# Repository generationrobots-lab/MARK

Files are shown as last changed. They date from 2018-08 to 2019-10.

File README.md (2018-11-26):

# M.A.R.K

M.A.R.K est un robot modulaire destiné à l'apprentissage. La carte [Arduino Mega] et la librairie fournie permettent une utilisation simple des principaux modules. L'[IDE Arduino] procure les outils nécessaires pour programmer le micro-contrôleur de la carte [Arduino Mega], le celèbre [ATmega2560]. 

[IDE Arduino]: https://www.arduino.cc/en/Main/Software/
[Arduino Mega]:https://www.generationrobots.com/fr/401945-arduino-mega-2560-rev3.html
[ATmega2560]: http://ww1.microchip.com/downloads/en/devicedoc/atmel-2549-8-bit-avr-microcontroller-atmega640-1280-1281-2560-2561_datasheet.pdf

## Installation

### IDE Arduino
Page de téléchargement : <br />
https://www.arduino.cc/en/Main/Software

Tutoriels d'installation : <br />
https://www.arduino.cc/en/Guide/Windows<br />
https://www.arduino.cc/en/Guide/Linux <br />
Le paquet Arduino est également présent dans les dépôts Universe d'Ubuntu.

### M.A.R.K librairie

1. [Télécharger le git](https://github.com/generationrobots-lab/MARK/archive/master.zip)
2. Décompresser l'archive et la placer dans un répertoire de votre choix.
3. Lancer l'IDE Arduino 
4. Dans  `Fichier => Préférences => Paramètres`, le champ "Emplacement du carnet de croquis" doit pointer vers le dossier "Software" de l'archive fraîchement décompressée et rangée (exemple : D:\MARK-master\Software)
5. Dans l'IDE Arduino, vous devriez voir apparaitre dans `Ficher => Exemples => MARK` les exemples pour débuter avec votre M.A.R.K.

Il est également possible de fusionner le dossier Software avec le dossier que vous utilisez déjà (par defaut C:\Users\..\Documents\Arduino).

## Code d'exemple 

```c++
#include <MARK.h>

MARK myrobot; //initialize an instance of the class

void setup() {
  myrobot.begin();
  delay(50);
  myrobot.setLeftMotor(50);
  myrobot.setRightMotor(50);
  delay(3000); //forward 3s
  myrobot.stopLeftMotor();
  myrobot.stopRightMotor();
}

void loop() {
  //nothing
  delay(300);
}

```

## Documentation
Pour plus d'informations, merci de consulter le [wiki.](https://github.com/generationrobots-lab/MARK/wiki)

## Developement

### Contribution

Pour toute contribution au maintien ou à l'amélioration de la librairie, merci de faire un "pull request".  <br />
Pour remonter des problèmes, merci d'ouvrir un ticket dans les "issues".

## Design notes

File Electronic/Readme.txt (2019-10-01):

YOu need to import all of libreries in your eagle folder and after open the schematic MARK.sch

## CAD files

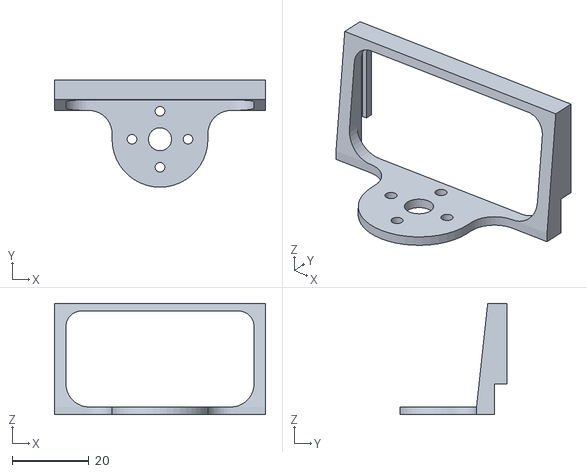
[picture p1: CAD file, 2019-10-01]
3D_model/US_Support.STL
55.0 x 28.0 x 29.0

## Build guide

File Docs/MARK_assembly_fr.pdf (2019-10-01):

# M.A.R.K

### By Génération Robots

10/09/2018

# Documentation de montage

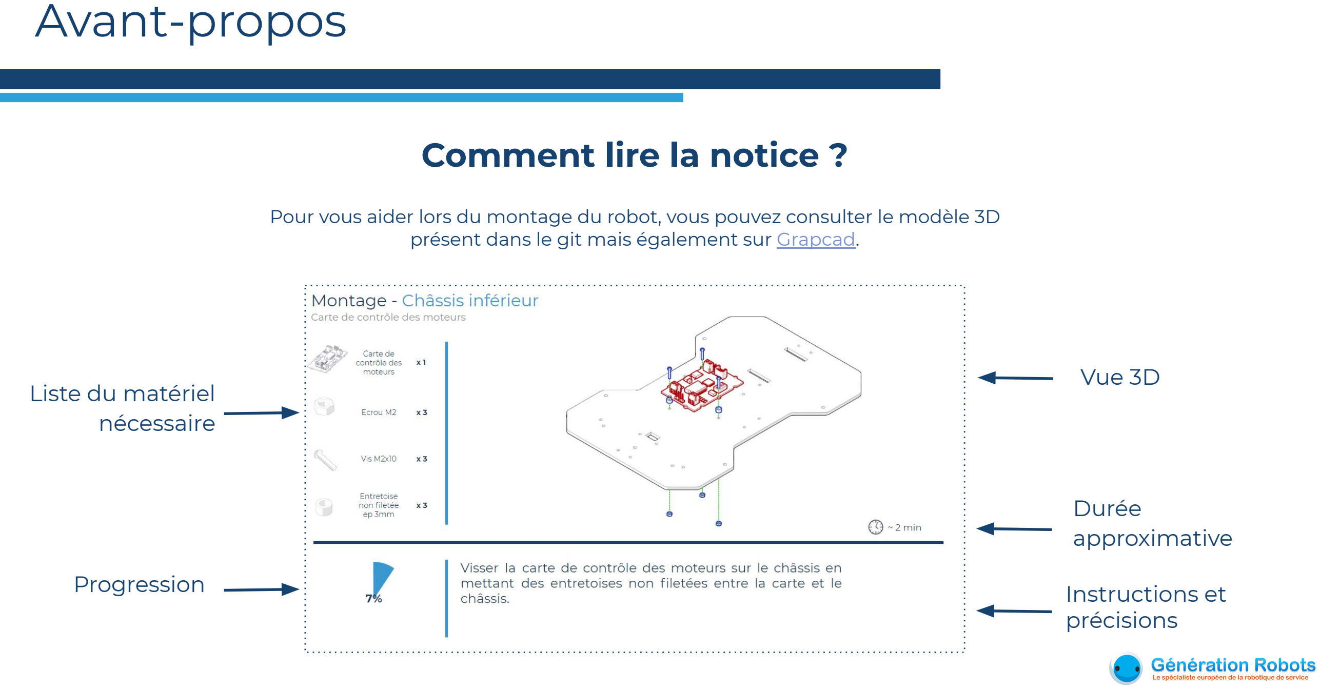
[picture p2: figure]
Avant-propos; Comment lire la notice ?; Instructions et précisions; Vue 3D; Durée approximative; Progression; Liste du matériel nécessaire

Pour vous aider lors du montage du robot, vous pouvez consulter le modèle 3D présent dans le git mais également sur Grapcad. (https://grabcad.com/library/m-a-r-k-1)

### Montage - Châssis inférieur

Vue globale

3

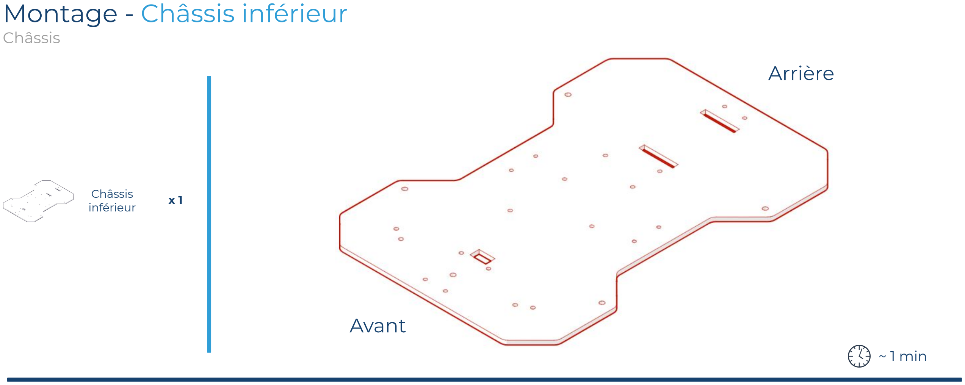
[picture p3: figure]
~ 1 min; Châssis; inférieur; Avant; Arrière; Montage - Châssis inférieur

Prendre le châssis inférieur.
Pour repérer le sens, la gravure dans le coin est à l’arrière gauche du robot et est dans le bon sens de lecture si on se place au dessus du châssis.

2%

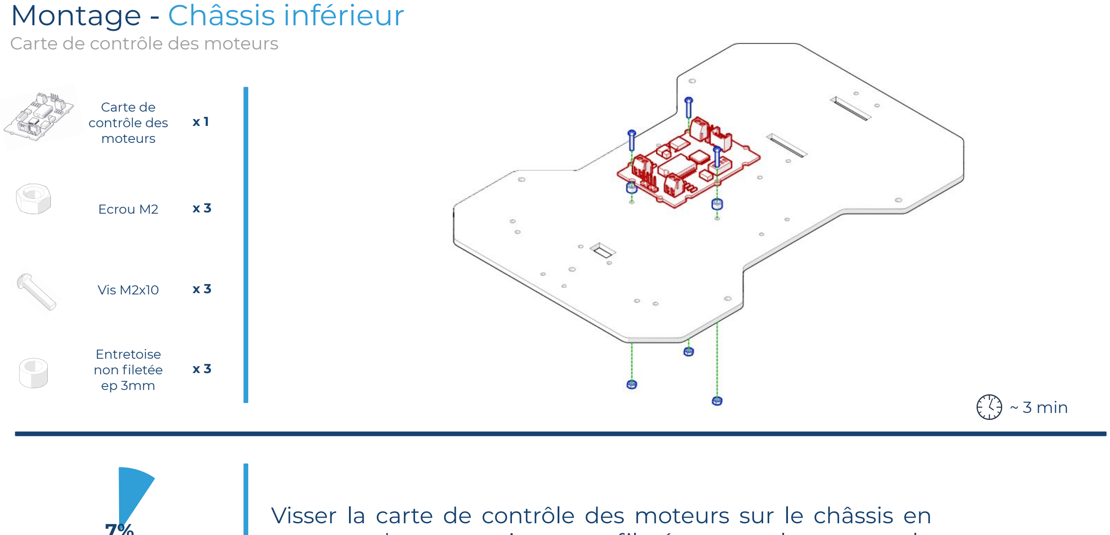
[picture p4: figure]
Montage - Châssis inférieur; Carte de contrôle des moteurs; ~ 3 min; Ecrou M2; Vis M2x10; Entretoise non filetée ep 3mm

Visser la carte de contrôle des moteurs sur le châssis en mettant des entretoises non filetées entre la carte et le châssis.

7%

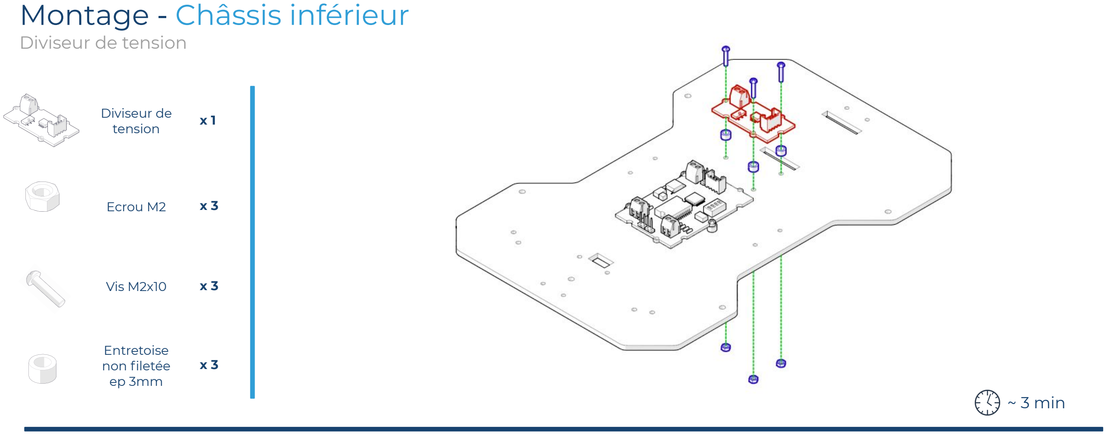
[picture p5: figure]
Diviseur de; tension; ~ 3 min; Entretoise non filetée ep 3mm; Montage - Châssis inférieur; Diviseur de tension; Ecrou M2; Vis M2x10

Visser le diviseur de tension sur le châssis en mettant des entretoises non filetées entre la carte et le châssis.
12%

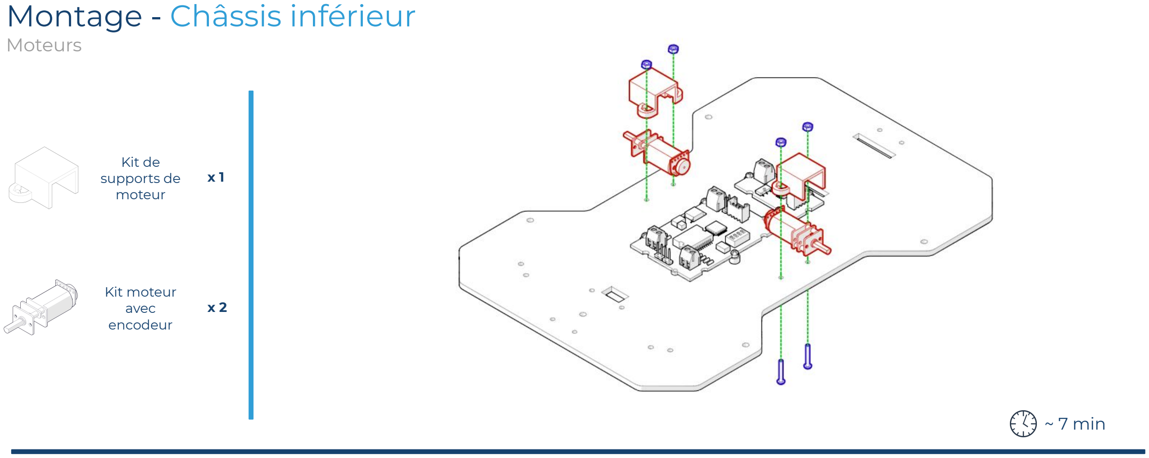
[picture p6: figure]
Kit de supports de moteur; ~ 7 min; Kit moteur avec encodeur; Montage - Châssis inférieur; Moteurs

Fixer les moteurs à l’aide des supports.
Les encoches à l'intérieur du support correspondent aux plaques présentes dans la partie réducteur du moteur. Placer l’écrou dans le logement prévu à cet effet dans le support avant de visser.

18%

Brancher les moteurs (via les encodeurs) sur la carte de contrôle des moteurs.

Retirer le jumper (J4) et vérifier l’adresse I2C.

18%

~ 5 min

### Montage - Châssis supérieur

Câblage

Monter les roues sur les moteurs.

20%

~ 2 min

x 2 Roue
60 x 8mm

### Montage - Châssis inférieur

Roues motrices

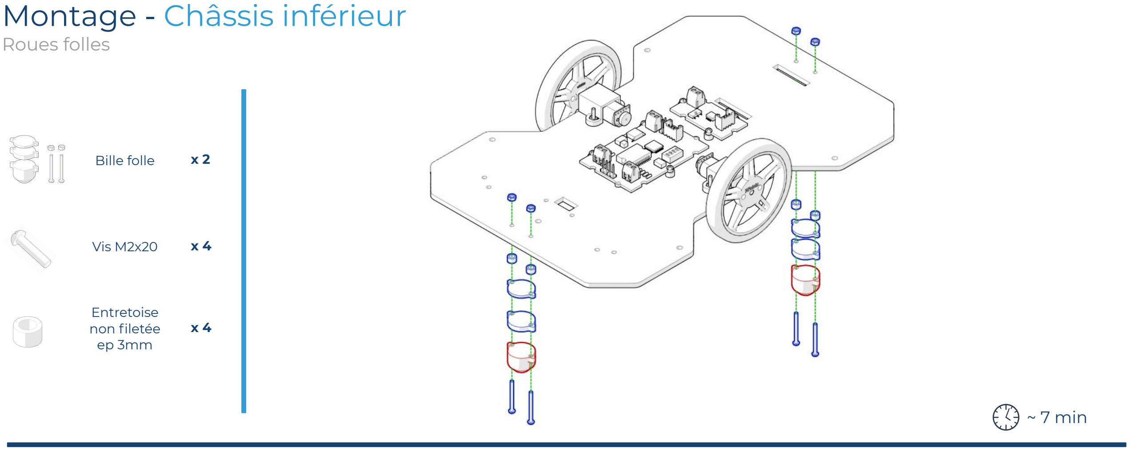
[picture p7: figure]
Bille folle; ~ 7 min; Entretoise non filetée ep 3mm; Vis M2x20; Montage - Châssis inférieur; Roues folles

Monter les billes sous le châssis en utilisant tous les éléments présents dans le sachet et deux entretoises non filetées (ep 3mm).
25%

### Montage - Châssis inférieur

Microrupteurs

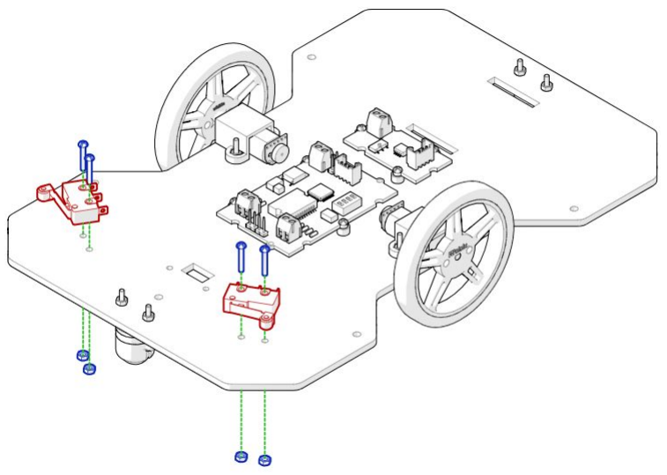
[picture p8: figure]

Visser les microrupteurs sur le châssis en prenant soin que les galets soient tournés vers l'extérieur du robot.

~ 4 min

30%

microrupteur x 2

x 4

Ecrou M2 x 4

Vis M2x6

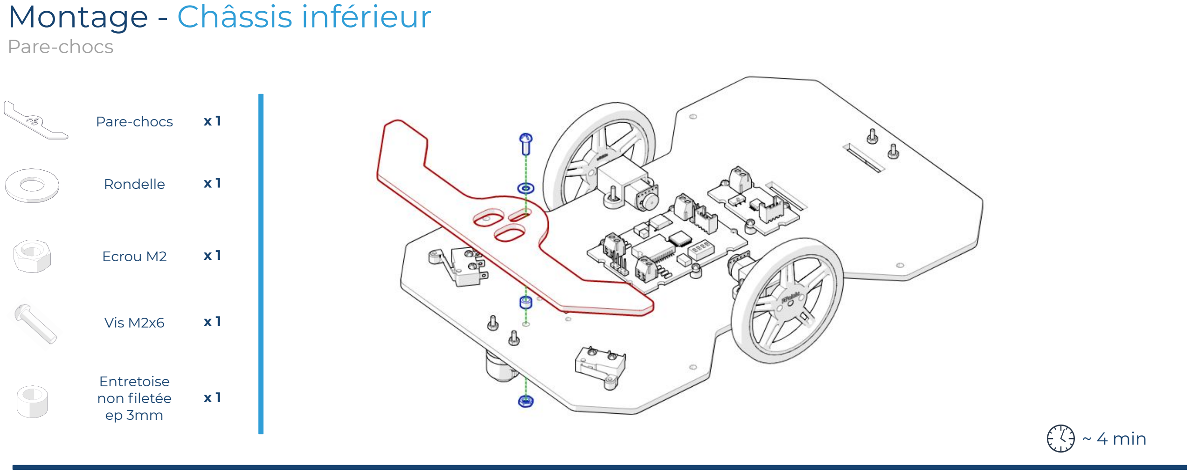
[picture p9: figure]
Rondelle; ~ 4 min; Ecrou M2; Vis M2x6; Entretoise non filetée ep 3mm; Montage - Châssis inférieur; Pare-chocs

Monter le pare-choc en mettant une entretoise non filetée dans le trou oblong, la rondelle par dessus et enfin visser le tout. le pare-choc doit rester mobile.
30%

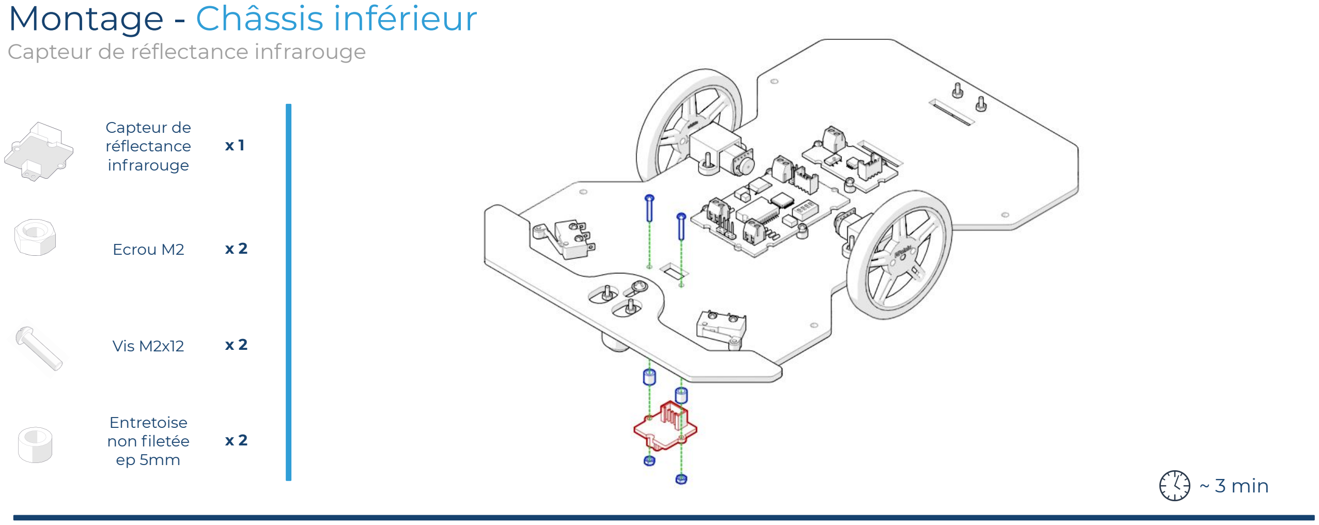
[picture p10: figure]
Capteur de réflectance infrarouge; ~ 3 min; Ecrou M2; Vis M2x12; Entretoise non filetée ep 5mm; Montage - Châssis inférieur

Visser le capteur de réflectance infrarouge sous le châssis en mettant des entretoises non filetées entre la carte et le châssis.
34%

Visser les grandes entretoises filetées au châssis.

~ 2 min

### Montage - Châssis inférieur

Entretoises

36%

Entretoise M3
F/F 60mm | x 4
Vis M3 x 8mm | x 4

### Montage - Châssis supérieur

Vue globale

15

### Montage - Châssis supérieur

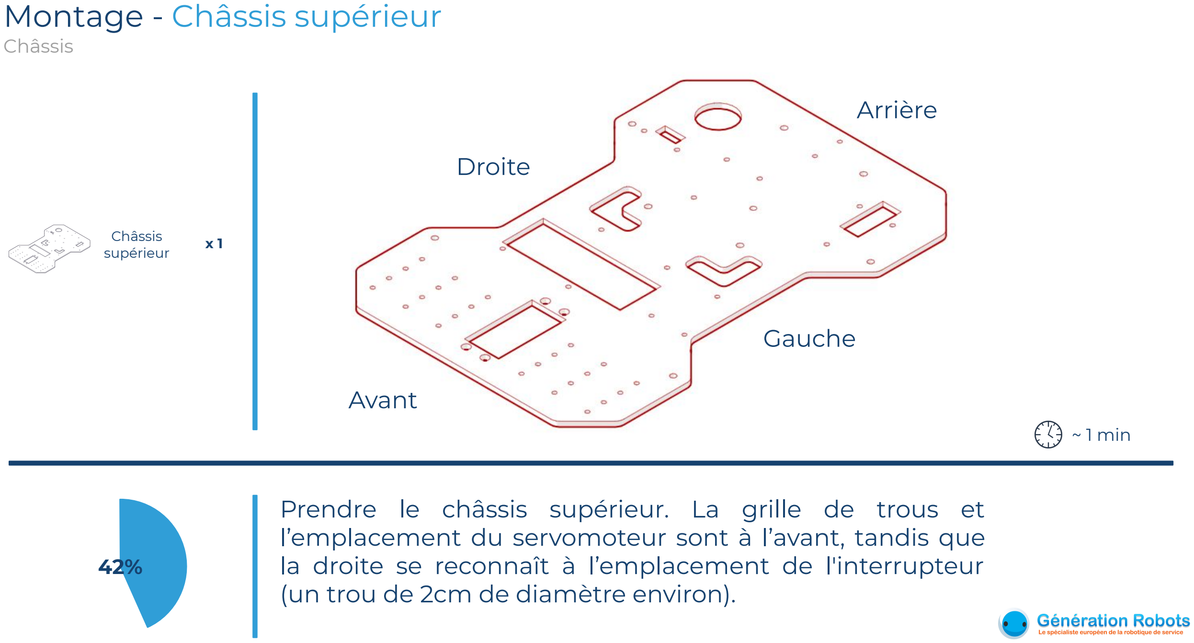
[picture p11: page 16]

Prendre le châssis supérieur. La grille de trous et l’emplacement du servomoteur sont à l’avant, tandis que la droite se reconnaît à l’emplacement de l'interrupteur (un trou de 2cm de diamètre environ).

~ 1 min

Châssis

Avant

Arrière

Droite

Gauche

42%

Châssis
supérieur x 1

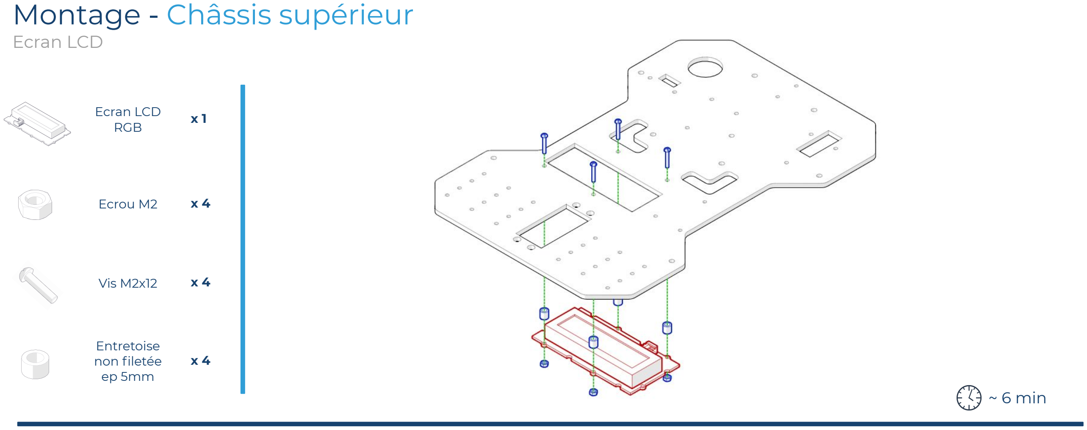
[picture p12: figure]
Ecran LCD RGB; ~ 6 min; Ecrou M2; Vis M2x12; Entretoise non filetée ep 5mm; Montage - Châssis supérieur; Ecran LCD

Connecter | le | câble | avant | de | monter | l’écran.

Visser l’écran LCD sous le châssis en mettant des entretoises non filetées entre la carte et le châssis.

47%

Visser le module wifi sous le châssis, les composants vers le bas.

~ 4 min

### Montage - Châssis supérieur

Module Wifi

51%

Module wifi x 1

x 3

Ecrou M2 x 4

Vis M2x6

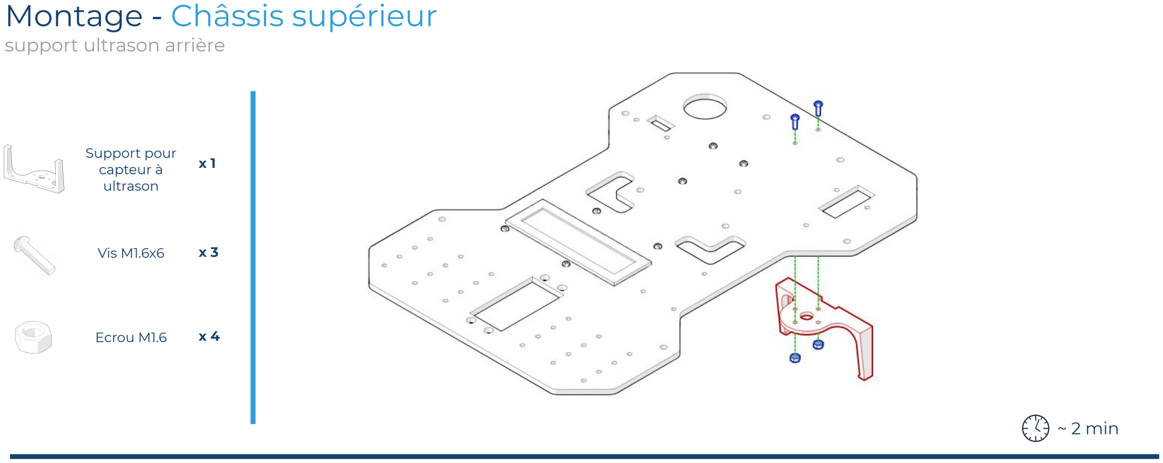
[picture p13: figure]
~ 2 min; Montage - Châssis supérieur; support ultrason arrière; Support pour capteur à ultrason; Ecrou M1.6; Vis M1.6x6

Visser un premier support pour capteur à ultrason à l’arrière du robot.
55%

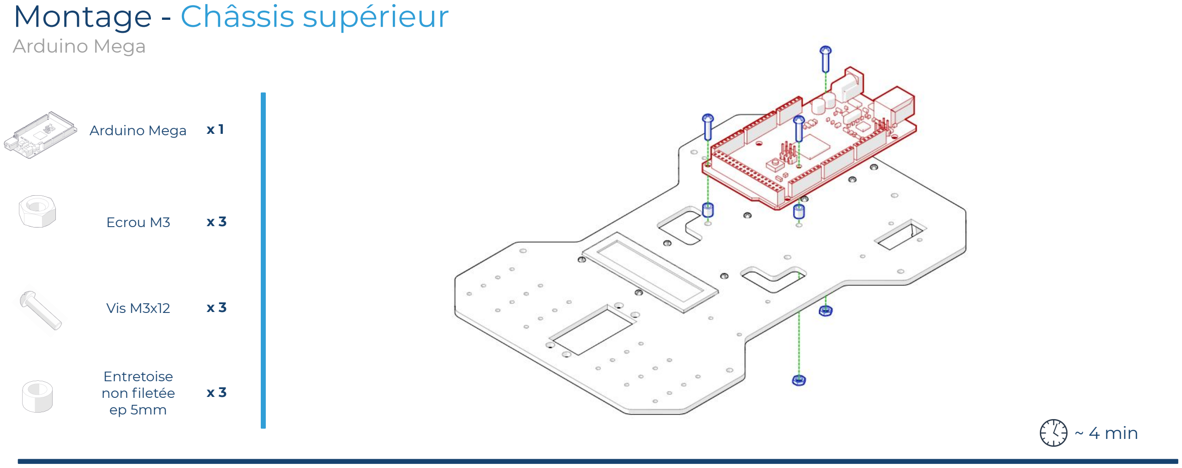
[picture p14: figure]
Arduino Mega; ~ 4 min; Ecrou M3; Vis M3x12; Entretoise non filetée ep 5mm; Montage - Châssis supérieur

Visser l’arduino mega sur le châssis en mettant des entretoises non filetées entre la carte et le châssis.
60%

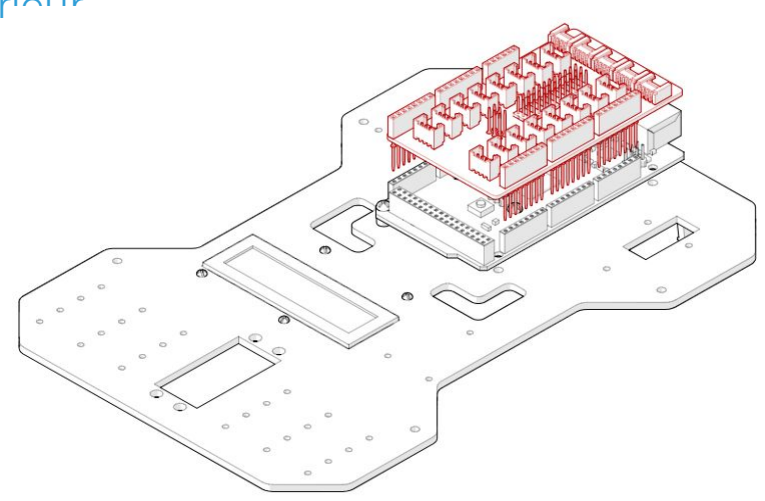
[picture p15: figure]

Mettre en place le grove mega shield sur l’arduino mega en s’assurant que les broches correspondent.

~ 1 min

### Montage - Châssis supérieur

Mega Shield

65%

Mega Shield x 1

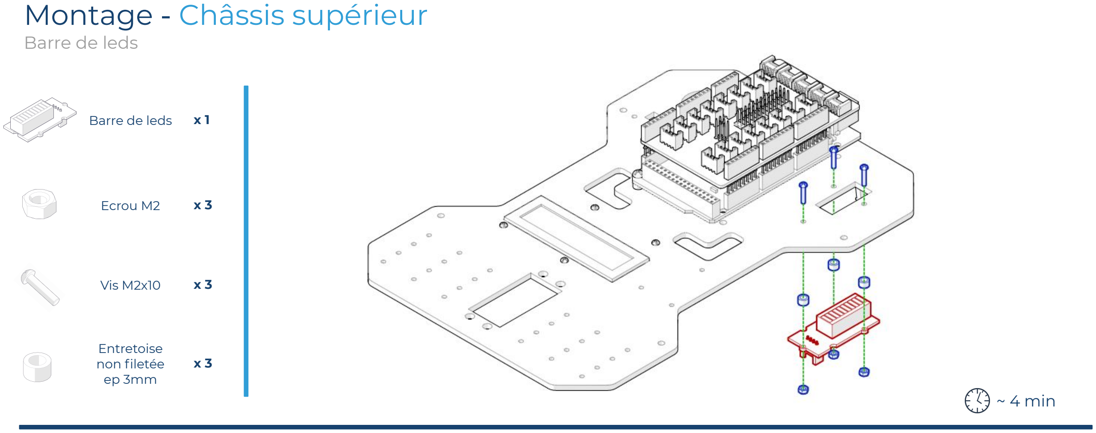
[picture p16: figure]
Barre de leds; ~ 4 min; Ecrou M2; Vis M2x10; Entretoise non filetée ep 3mm; Montage - Châssis supérieur

Visser la barre de leds sous le châssis en mettant des entretoises non filetées entre la carte et le châssis.
70%

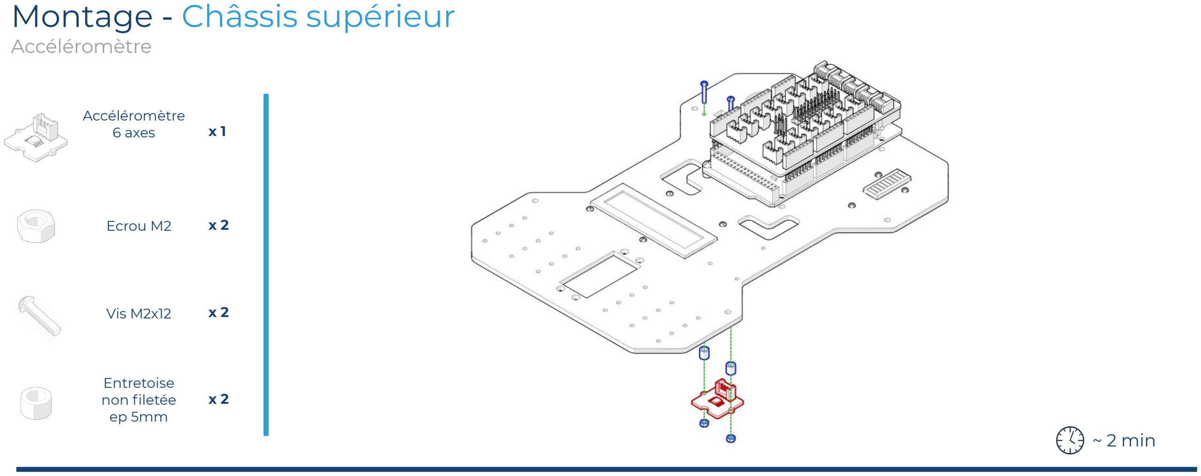
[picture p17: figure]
Accéléromètre 6 axes; ~ 2 min; Ecrou M2; Vis M2x12; Entretoise non filetée ep 5mm; Montage - Châssis supérieur; Accéléromètre

Visser l'accéléromètre sous le châssis en mettant des entretoises non filetées entre la carte et le châssis.
73%

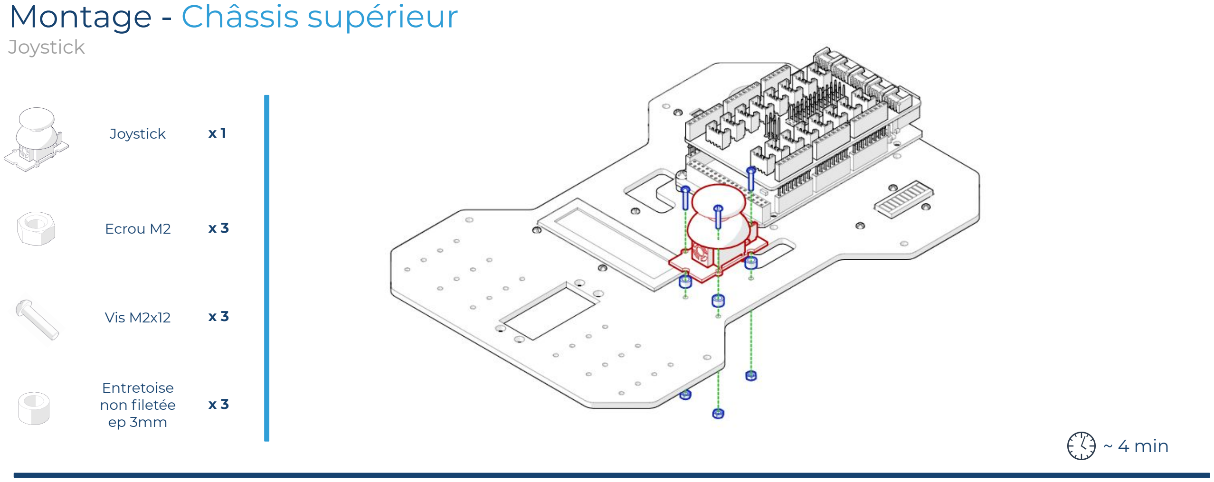
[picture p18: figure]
Joystick; ~ 4 min; Ecrou M2; Vis M2x12; Entretoise non filetée ep 3mm; Montage - Châssis supérieur

Visser le joystick sur le châssis en mettant des entretoises non filetées entre la carte et le châssis.
78%

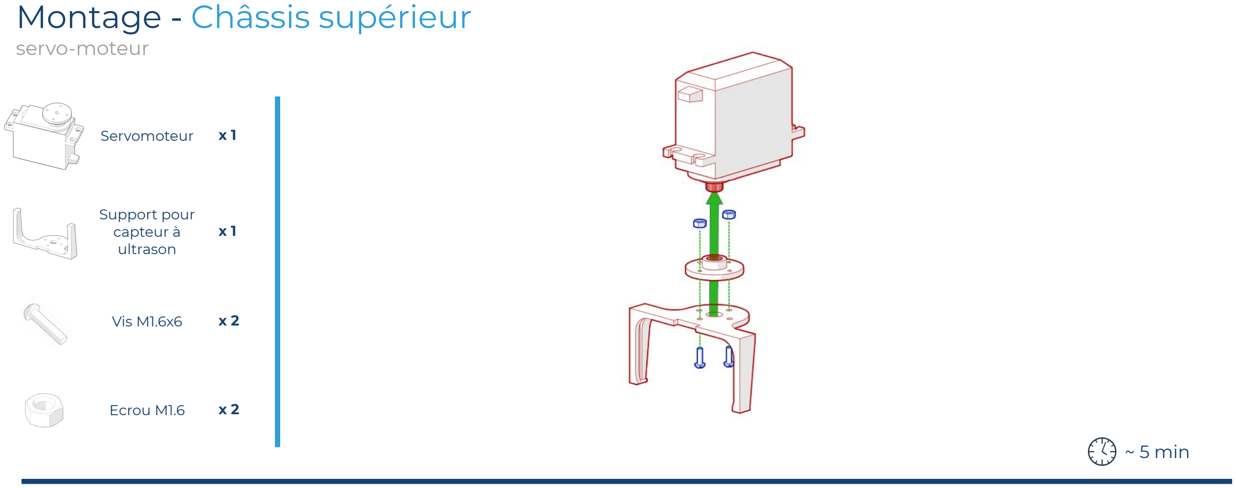
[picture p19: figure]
Servomoteur; ~ 5 min; Support pour capteur à ultrason; Vis M1.6x6; Ecrou M1.6; Montage - Châssis supérieur; servo-moteur

Visser un support du capteur à ultrason sur le palonnier du servo-moteur. Visser le palonnier sur le servo à l’aide de la vis fournie avec le servo-moteur.
82%

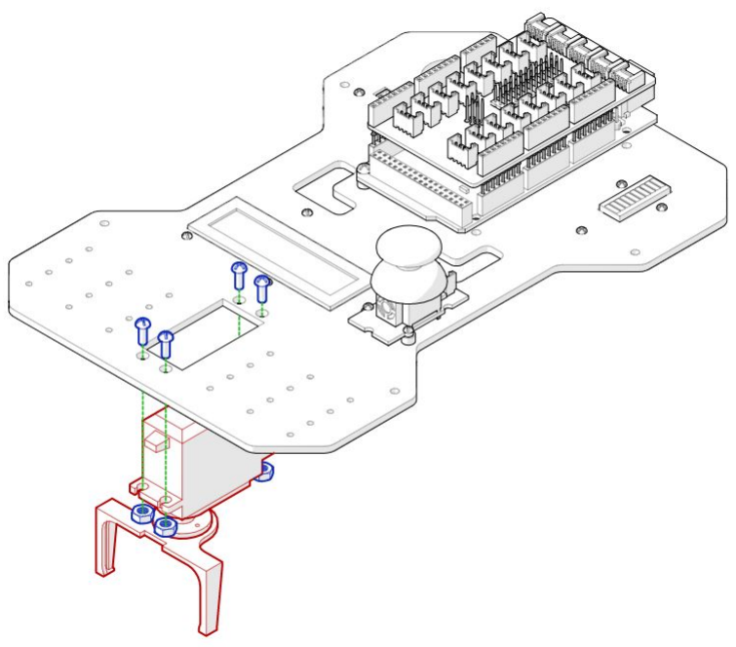
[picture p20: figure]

Visser le servo-moteur précédemment assemblé sur le châssis.
86%

~ 4 min

### Montage - Châssis supérieur

servo-moteur

Ecrou M3 | x 4
Vis M3 x 8mm | x 4

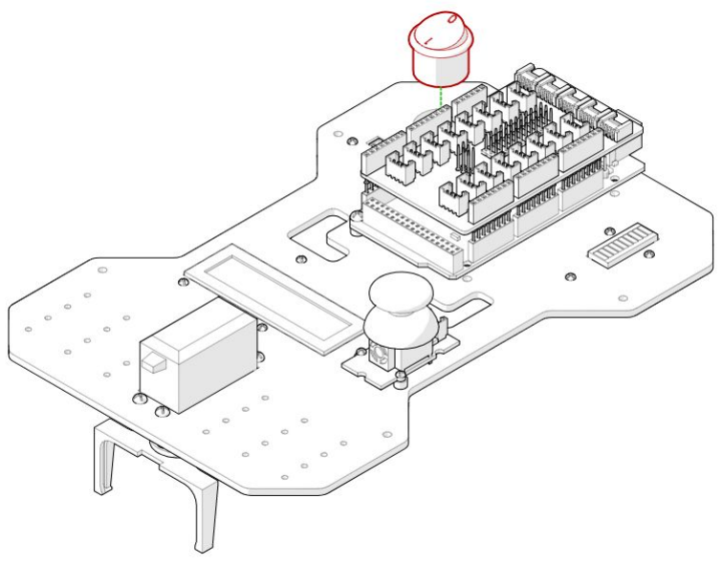
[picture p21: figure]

Faire passer les câbles soudés à l’interrupteur avant de mettre ce dernier à sa place. L’orientation de l’interrupteur
91% | est libre.

~ 2 min

### Montage - Châssis supérieur

Interrupteur

Interrupteur x 1

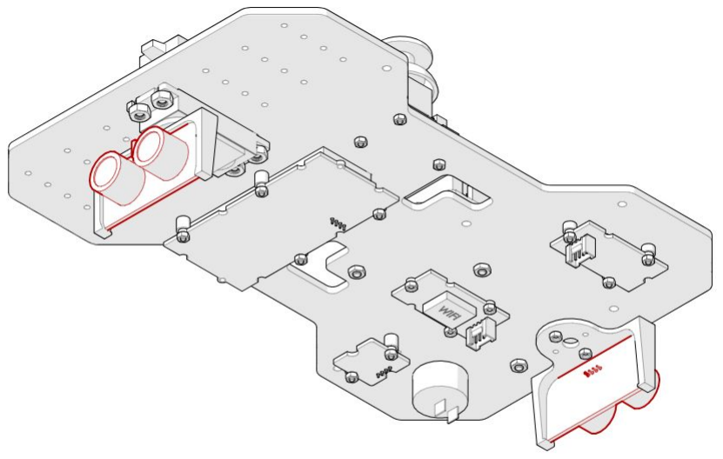
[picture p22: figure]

Mettre les capteurs à ultrasons dans les supports, le connecteur vers le haut.
95%

~ 2 min

### Montage - Châssis supérieur

Capteurs à ultrason

x 2 Capteur à
ultrason

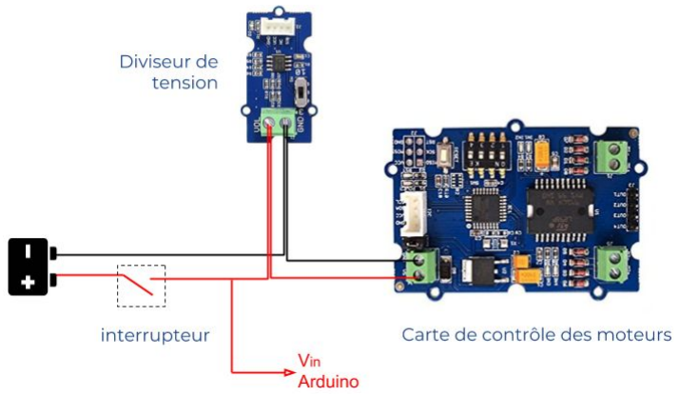
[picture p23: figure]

Brancher le câble d’alimentation (celui soudé à l’interrupteur) au diviseur de tension, puis à la carte de contrôle des moteurs à l’aide des borniers présents sur les cartes. Connecter le câble jumper à la carte arduino (Vin).

95%

~ 8 min

### Montage - Châssis supérieur

Câblage

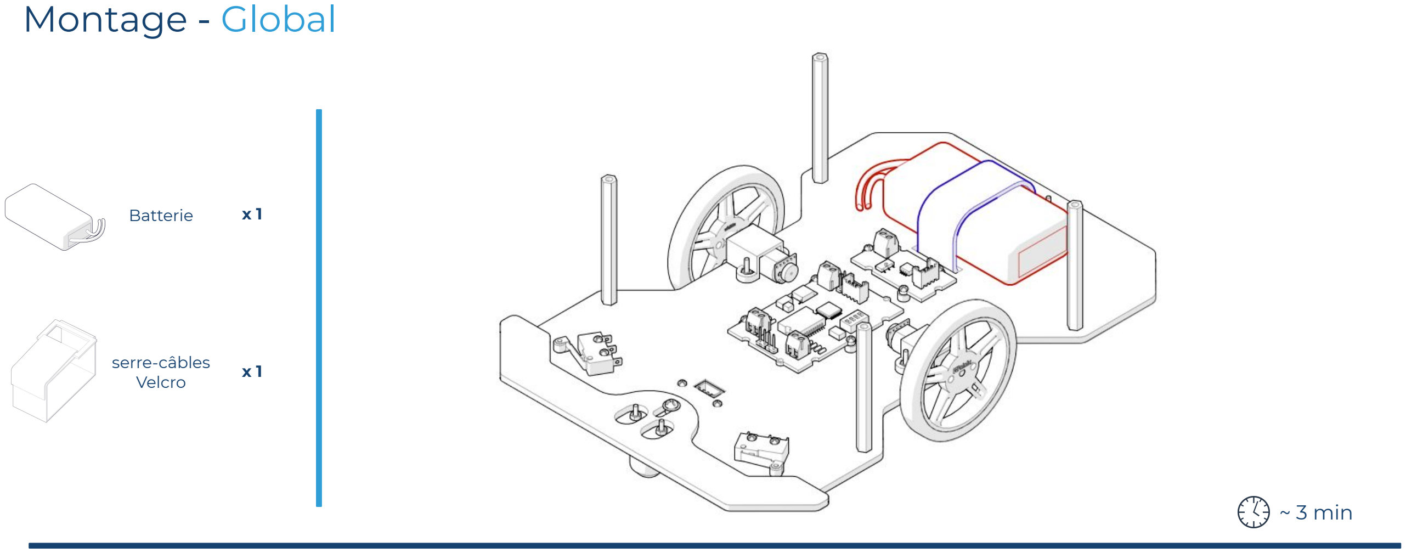
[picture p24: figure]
~ 3 min; Montage - Global; Batterie; x 1 serre-câbles Velcro

Vérifier que l’interrupteur est bien en position éteint (0). Placer la batterie sur le châssis, la brancher sur le connecteur en T, et mettre le serre-câbles Velcro pour la maintenir en place.

97%

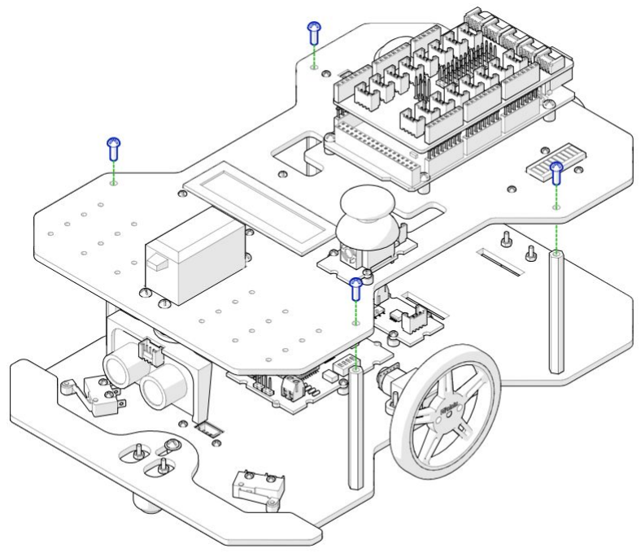
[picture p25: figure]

Assembler ensemble les deux parties. Vous pouvez alors finaliser le câblage à l’aide du wiki [lien] (https://github.com/generationrobots-lab/MARK/wiki/%C3%89lectronique)
100%

~ 2 min

### Montage - Global

Vis M3 x 8mm x 4

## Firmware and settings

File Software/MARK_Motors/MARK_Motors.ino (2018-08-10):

/*
   Description : the robot advances until collision, and then backs off and turns, and advances again.
   more info about I2C motor driver : http://wiki.seeedstudio.com/Grove-I2C_Motor_Driver_V1.3/
*/
#include "Grove_I2C_Motor_Driver.h"

#define I2C_ADDRESS 0x0f

void setup() {
  Motor.begin(I2C_ADDRESS);
  delay(10);
  Motor.stop(MOTOR1);
  Motor.stop(MOTOR2);
  delay(1000);
}

void loop() {
  Motor.speed(MOTOR1, 30);
  Motor.speed(MOTOR2, 30);
  delay(1000);
  Motor.stop(MOTOR1);
  Motor.stop(MOTOR2);
  delay(1000);
  Motor.speed(MOTOR1, -30);
  Motor.speed(MOTOR2, -30);
  delay(1000);
  Motor.stop(MOTOR1);
  delay(1000);
}

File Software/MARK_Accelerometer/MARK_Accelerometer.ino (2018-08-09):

/*
   Description : This code displays the X accelerometer value on LCD screen
   press bumper right and left to change the value printed on LCD screen

   more informations : http://wiki.seeedstudio.com/Grove-6-Axis_AccelerometerAndGyroscope/
   this sensor use IMU's sparkfun library you can find it here : https://learn.sparkfun.com/tutorials/lsm6ds3-breakout-hookup-guide
  
   wiki LCD : http://wiki.seeedstudio.com/Grove-LCD_RGB_Backlight/
   wiki wire : https://www.arduino.cc/en/reference/wire
*/

#include <Wire.h>
#include "SPI.h"
#include "SparkFunLSM6DS3.h"
#include "rgb_lcd.h"

rgb_lcd lcd;
LSM6DS3 myIMU( I2C_MODE, 0x6A );  //I2C device address 0x6A
const byte bumperLeft = 2;
const byte bumperRight = 3;
volatile byte stateBumperLeft = LOW;
volatile byte stateBumperRight = LOW;

volatile long left_timestamp = 0; //used to stamp start time of an IR pulse
volatile long left_timestampdiff = 0; //used to stamp start time of an IR pulse

volatile long right_timestamp = 0; //used to stamp start time of an IR pulse
volatile long right_timestampdiff = 0; //used to stamp start time of an IR pulse

volatile int case_var = 0; //used to stamp start time of an IR pulse


void setup()
{
  lcd.begin(16, 2); //init lcd
  lcd.setRGB(100, 100, 150); //set color to blue

  pinMode(bumperLeft, INPUT_PULLUP);
  pinMode(bumperRight, INPUT_PULLUP);

  attachInterrupt(digitalPinToInterrupt(bumperLeft), leftCB, FALLING); // Call leftCB() when bumper Left is pulled
  attachInterrupt(digitalPinToInterrupt(bumperRight), rightCB, FALLING);// Call rightCB() when bumper Right is pulled

  lcd.setCursor(0, 0);

  if ( myIMU.begin() != 0 )// test if IMU is started
  {
    lcd.print("Device error");
  }
  else
  {
    lcd.print("Device OK!");
  }
  delay(2000);
  lcd.clear();
}


void loop()
{
  lcd.setCursor(0, 0); // places the cursor in the top left corner
  switch (case_var) {  // display datas
    case 0:
      lcd.print("Accel X  ");
      lcd.setCursor(0, 1);
      lcd.print(myIMU.readFloatAccelX(), 4);
      break;
    case 1:
      lcd.print("Accel Y  ");
      lcd.setCursor(0, 1);
      lcd.print(myIMU.readFloatAccelY(), 4);
      break;
    case 2:
      lcd.print("Accel Z  ");
      lcd.setCursor(0, 1);
      lcd.print(myIMU.readFloatAccelZ(), 4);
      break;
    case 3:
      lcd.print("Gyro X  ");
      lcd.setCursor(0, 1);
      lcd.print(myIMU.readFloatGyroX(), 4);
      break;
    case 4:
      lcd.print("Gyro Y  ");
      lcd.setCursor(0, 1);
      lcd.print(myIMU.readFloatGyroY(), 4);
      break;
    case 5:
      lcd.print("Gyro Z  ");
      lcd.setCursor(0, 1);
      lcd.print(myIMU.readFloatGyroZ(), 4);
      break;
    case 6:
      lcd.print("Temp     ");
      lcd.setCursor(0, 1);
      lcd.print(myIMU.readTempC(), 4);
      break;
    default:
      lcd.print("Error ..   ");
      break;
  }
  delay(250);
}
void rightCB() { //decrasses case_var value to switch the display in loop()
  right_timestampdiff =  micros() - right_timestamp ;
  if (right_timestampdiff > 1000000)
  {
    if (case_var <= 0) {
      case_var = 0;
    }
    else {
      case_var -= 1;
    }
    right_timestamp = micros() ;

  }
}

void leftCB() { //incrasses case_var value to switch the display in loop()
  left_timestampdiff =  micros() - left_timestamp ;
  if (left_timestampdiff > 1000000)
  {
    if (case_var >= 6) {
      case_var = 6;
    }
    else {
      case_var += 1;
    }
    left_timestamp = micros() ;

  }
}

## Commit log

2018-08-09 Start the project
    [US_Support.STL]
2018-08-10 Add motors function
2018-08-17 add some functions in lib (infrared, Battery, Ultrasonic, Bumper). and modify ino file to test new function.
2018-08-20 adding some function in library like : - Joystick (get X, Y and clic) - Servo motor (set and get pos) - Accelerometer (get acce X,Y,Z and Gyro X,Y,Z, and the temperature) - Encoder(get and reset) For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
    Next step is to implement WIFI and modify keyword
2018-08-21 add interruption flag
2018-08-27 add sensor test in function test()
2018-09-21 update assembly guide
2018-12-06 Add Buzzer and change servo pin
2019-04-05 Improve ultrasonic support
    [US_Support.STL]
2019-04-05 improve utrasonic support
    [US_Support.STL]
2019-04-05 Electronics files added Re mane libraries to Libraries
    [MARK.sch]
2019-04-05 ultrasonic cm to mm
